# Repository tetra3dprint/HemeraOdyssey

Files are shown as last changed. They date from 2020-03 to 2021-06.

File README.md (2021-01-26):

## HemeraOdyssey **BETA** (v1.0)
Universal E3D Hemera mod for the Prusa i3 MK2 MK2.5 MK2.5S MK3 MK3S + Other variants  
This is for advanced users so **please** fully read this [**README.md**](README.md) to avoid disappointment, frustration and missguided expectations!  
I make no claims about this mod, it simply satisfies the requirement of enabling the Hemera to be used on stock firmware, pass self test and XYZ calibration.

[F **HemeraOdyssey Facebook group**](https://www.facebook.com/groups/HemeraOdyssey/)

Find me on twitter @ [tetra3dprint](https://twitter.com/tetra3dprint) 

## What is this mod
This is a universal one fits all mod that enabled the use of the E3D Hemera extruder on a Prusa i3 MK2/S MK2.5/S MK3/S without needing custom firmware (sort of).  
It will pass the self-test and XYZ calibration thanks to the geometry matching the stock setup but needs a minimum change to the e-steps that can be done via gcode.  
There is no loss in build volume.  
It supports both Laser and IR filament sensors.  
This is a very maintainable and moddable mod. I encourage and look forward to seeing mods and remixes, remeber to use the tag #hemeraodyssey

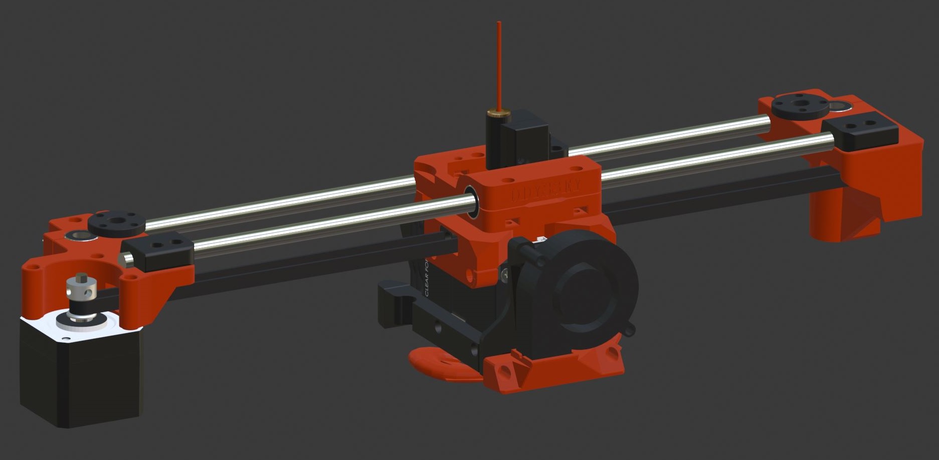
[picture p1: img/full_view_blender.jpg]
Hemera Odyssey Full View
  

|Document|Link|
|---:|:---|
|BOM|[**BOM**](BOM_Condensed.md)|
|Blender Source|[**HemeraOdysseyBlenderFile.zip**](../../raw/master/HemeraOdysseyBlenderFile.zip)
|**please read** Printing Guide|[**Printing Guide**](Print_Settings.md)|
|Build guide|[**Build guide**](Build_Guide/00_First.md)|
|Want to support this mod?|[**Click me**](#lots-of-coffee-and-filament-consumption)|

## This is a **BETA** mod!
I have to stress this is a **beta** mod with beta documentation.  
Parts might change over the next few weeks, please check everything and don't assume.  
I will make a note of changes in the assembly guide where relevant.  
You can also check for listed changes [**here**](Build_Guide/00_First.md#changes-in-beta-printed-parts)  
  
Documentation is not complete and will be updated daily until this message is gone.  
There are probably spelling and grammar mistakes and possibly incorrect links and numbers.   
Field testing of parts and printing parts is **limited**.
Some parts might cause problems when printing especially with materials I haven't tested.
I will attempt to deal with any highlighted issue in a timely fasion, that said, changes will be kept to a minimum if possible.

## Please respect the [**LICENSE**](LICENSE) this mod is released under
Please respect the GNU General Public License v3.0 that this mod is released under. This is the same license that Prusa use.

## MMU2 Support?
Not yet supported, however it is intended, but will require custom modified firmware which will come at a later date.

## No custom firmware (sort of)???!!!
Aside from needing to change the e-steps, this will work with stock firmware but it's not ideal.
The menu unload can cause a blob of filament to be pinched off below the hobbed gears. This in turn causes a filament jam that would then need clearing by dismantling the extruder.
On the MK3, the e-current will need to be increased slightly because the motor is 1.3A vs stock at 1.0A otherwise a moiré pattern is more visible than usual.

## Caveats
I showed a preview of my mod and there was a voice of concern in regard to the center of mass moving forward on the X carriage.  
This was mainly because the X motor is now positioned forward compared to stock.  
The concern is that this now unfavorably loads the z axis bearing and in turn reduces the life of the bearings and smooth rods.  
I have not been able to find data that supports or refutes this concern, however it does appear that the extra loading is within spec.  
So what does this mean? It might, or might not reduce the life of your z axis bearings and smooth rods.

The x carriage is slightly heavier than stock so this could manifest as more ghosting from x movements. Print settings can be adjusted to counter this.  
Here is a weight comparison of fully assembled variants of extruders: -  
|Extruder|~Weight(g)|
|---:|---:|
|Bondtech MK3|567|
|Stock MK2.5|630|
|Hemera Odyssey|697|

## Lots of coffee and filament consumption
In making this mod I've used several rolls of filament and drank lots of Grumpy Mule coffee. If you like it and want to support me in some way (obviously no obligation) maybe consider [**buying me a coffee here :)**](https://www.buymeacoffee.com/tetra3dprint)    

## Huge thanks to  
 
[Vlastimil Hovan on twitter](https://twitter.com/Vlastimil_Hovan)  
Vlastimil has kindly beta tested my mod, printed several variations and tried them out on his machines. He has also has given invaluable suggestions and feedback that have made their way back into the design.  
Not only that but he has created the first official mod (Z Tops) for my mod that enables the use on the MK3S variant, so huge respect and thanks to him.  
   
[Grégoire Saunier #BearUpgrade on twitter](https://twitter.com/GregoireSaunier)  
Grégoire has not only been inspiration but has also been kind enough to offer some guidance here and there that kept me on the straight and narrow :) so huge respect and thanks to him. 

## Blender Source Files
I used Blender to create the files for this mod so only the blender file and STL files will are available.  
The blender file is available at the root of this repo here [**HemeraOdysseyBlenderFile.zip**](../../raw/master/HemeraOdysseyBlenderFile.zip)

## Sources
* Prusa: http://www.prusa3d.com
* E3D Hemera: https://e3d-online.com/
* Grégoire Saunier : https://github.com/gregsaun/
* Blender 3D: https://www.blender.org/

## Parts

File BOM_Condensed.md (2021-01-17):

# Hemera Odyssey Beta

## Bill of Materials

### Hardware

| Part | Quantity | Detail | Example Links |
|---|:---:|---|---|
| Original Prusa i3 MK2(S) or MK2.5(S) or MK3(S) | 1 | :warning: MK2 or MK3 (non-S) also usable | [Prusa](https://www.prusa3d.com) |
| E3D Hemera Direct Kit (1.75mm) | 1 | | [E3D-ONLINE](https://e3d-online.com/collections/hotends/products/e3d-hemera-direct-kit-1-75mm)|
| M3x8mm socket head screw (ISO 4762) | 4 | | [McMaster-Carr](https://www.mcmaster.com/91292A112/) |
| M3x10mm socket head screw (ISO 4762) | 7 | | [McMaster-Carr](https://www.mcmaster.com/91292A113/) |
| M3x14mm socket head screw (ISO 4762) | 21| | [McMaster-Carr](https://www.mcmaster.com/91292A027/) |
| M3x16mm socket head screw (ISO 4762) | 2 | | [McMaster-Carr](https://www.mcmaster.com/91292A115/) |
| M3x18mm socket head screw (ISO 4762) | 9 | | [McMaster-Carr](https://www.mcmaster.com/91292A029/) |
| M3x25mm socket head screw (ISO 4762) | 2 | | [McMaster-Carr](https://www.mcmaster.com/91292A020/) |
| M3x40mm socket head screw (ISO 4762) | 1 | | [McMaster-Carr](https://www.mcmaster.com/91292A024/) |
| M3 hex nuts DIN 934 | 10| | [McMaster-Carr](https://www.mcmaster.com/91828A211/) |
| M3 square nut DIN 562 | 14| | [McMaster-Carr](https://www.mcmaster.com/97258A101/) |
| M3 thin square nut (Hemera) | 4 | | [E3D-ONLINE](https://e3d-online.com/products/e3d-hemera-fixings-kit) |
| M3 nylock nut DIN 985 | 6 | | [McMaster-Carr](https://www.mcmaster.com/93625a100) |
| M3 flat washer (ISO 7089) | 2 | | [McMaster-Carr](https://www.mcmaster.com/93475A210/) |
| Zip ties 2.5x100mm | 7 | | |
| 1.75mm PTFE Tube (43mm.L) | 1 | | |
| 1.75mm PTFE Tube (11mm.L) - Laser sensor | 1 | :warning: Only for MK2 or MK3 (non-S) | |
 
### Optional

| Part | Quantity | Detail | Example Links |
|---|:---:|---|---|
| 4.95mm OD Dowel (14-15.8mm) | 1 | for Gates Idler | |
| Toothed T20 Gates Idler | 1 | | |
| M5 Threaded Brass Insert | 1 | | |
 
### Printed Parts

| Part | Quantity | Comment |
|---|:---:|---|
| [Filament_Sensor_IR_Cover](HemeraOdyssey_STLs_BETA/HemeraOdyssey-Filament_Sensor_IR_Cover.stl) | 1 | :warning: Only for MK2.5(S) or MK3(S)|
| [Filament_Sensor_IR_Housing](HemeraOdyssey_STLs_BETA/HemeraOdyssey-Filament_Sensor_IR_Housing.stl) | 1 | :warning: Only for MK2.5(S) or MK3(S)|
| [Filament_Sensor_IR_Spring](HemeraOdyssey_STLs_BETA/HemeraOdyssey-Filament_Sensor_IR_Spring.stl) | 1 | :warning: Only for MK2.5(S) or MK3(S)|
| [Filament_Sensor_IR_Trigger](HemeraOdyssey_STLs_BETA/HemeraOdyssey-Filament_Sensor_IR_Trigger.stl) | 1 | :warning: Only for MK2.5(S) or MK3(S)|
| [Filament_Sensor_Laser_Housing](HemeraOdyssey_STLs_BETA/HemeraOdyssey-Filament_Sensor_Laser_Housing.stl) | 1 | |
| [Filament_Sensor_Laser_Lid](HemeraOdyssey_STLs_BETA/HemeraOdyssey-Filament_Sensor_Laser_Lid.stl) | 1 | |
| [Filament_Sensor_Laser_Wahser](HemeraOdyssey_STLs_BETA/HemeraOdyssey-Filament_Sensor_Laser_Wahser.stl) | 1 | |
| [Idler_Housing_Prusa](HemeraOdyssey_STLs_BETA/HemeraOdyssey-Idler_Housing_Prusa_20T_3mmID.stl) | 1 | |
| [Idler_Housing_Prusa_Bottom](HemeraOdyssey_STLs_BETA/HemeraOdyssey-Idler_Housing_Prusa_20T_3mmID_Spacer_Bottom.stl)| 1 | :warning: Print a single part|
| [Idler_Housing_Prusa_Top](HemeraOdyssey_STLs_BETA/HemeraOdyssey-Idler_Housing_Prusa_20T_3mmID_Spacer_Top.stl) | 1 | :warning: Print a single part|
| [Nozzle_Fang](HemeraOdyssey_STLs_BETA/HemeraOdyssey-Nozzle_Fang.stl) | 1 | :warning: Print a single part |
| [Part_Left_Front_Rod_Clamp](HemeraOdyssey_STLs_BETA/HemeraOdyssey-Part_Left_Front_Rod_Clamp.stl) | 1 | |
| [Part_Left_Motor](HemeraOdyssey_STLs_BETA/HemeraOdyssey-Part_Left_Motor.stl) | 1 | :warning: Print a single part |
| [Part_Right_Front_Rod_Clamp](HemeraOdyssey_STLs_BETA/HemeraOdyssey-Part_Right_Front_Rod_Clamp.stl) | 1 | |
| [Part_Right_Idler](HemeraOdyssey_STLs_BETA/HemeraOdyssey-Part_Right_Idler.stl) | 1 | :warning: Print a single part |
| [Undercarriage_Back](HemeraOdyssey_STLs_BETA/HemeraOdyssey-Undercarriage_Back.stl) | 1 | |
| [Undercarriage_Back_Cap](HemeraOdyssey_STLs_BETA/HemeraOdyssey-Undercarriage_Back_Cap.stl) | 1 | |
| [Undercarriage_Fan_Mount](HemeraOdyssey_STLs_BETA/HemeraOdyssey-Undercarriage_Fan_Mount.stl) | 1 | |
| [Undercarriage_Left](HemeraOdyssey_STLs_BETA/HemeraOdyssey-Undercarriage_Left.stl) | 1 | |
| [Undercarriage_Right](HemeraOdyssey_STLs_BETA/HemeraOdyssey-Undercarriage_Right.stl) | 1 | |
| [X_Carriage](HemeraOdyssey_STLs_BETA/HemeraOdyssey-X_Carriage.stl) | 1 | :warning: Print a single part |
| [X_Carriage_Belt_Tensioner_Left](HemeraOdyssey_STLs_BETA/HemeraOdyssey-X_Carriage_Belt_Tensioner_Left.stl) | 1 | |
| [X_Carriage_Belt_Tensioner_Right](HemeraOdyssey_STLs_BETA/HemeraOdyssey-X_Carriage_Belt_Tensioner_Right.stl) | 1 | |
| [X_Carriage_Washer](HemeraOdyssey_STLs_BETA/HemeraOdyssey-X_Carriage_Washer.stl) | 1 | :warning: Print a single part |
| [Z_Top_Left_7mm_MK3S_MK2_5S](HemeraOdyssey_STLs_BETA/HemeraOdyssey-Z_Top_Left_7mm_MK3S_MK2_5S.stl) | 1 | :warning: Only for MK2.5(S) or MK3(S)|

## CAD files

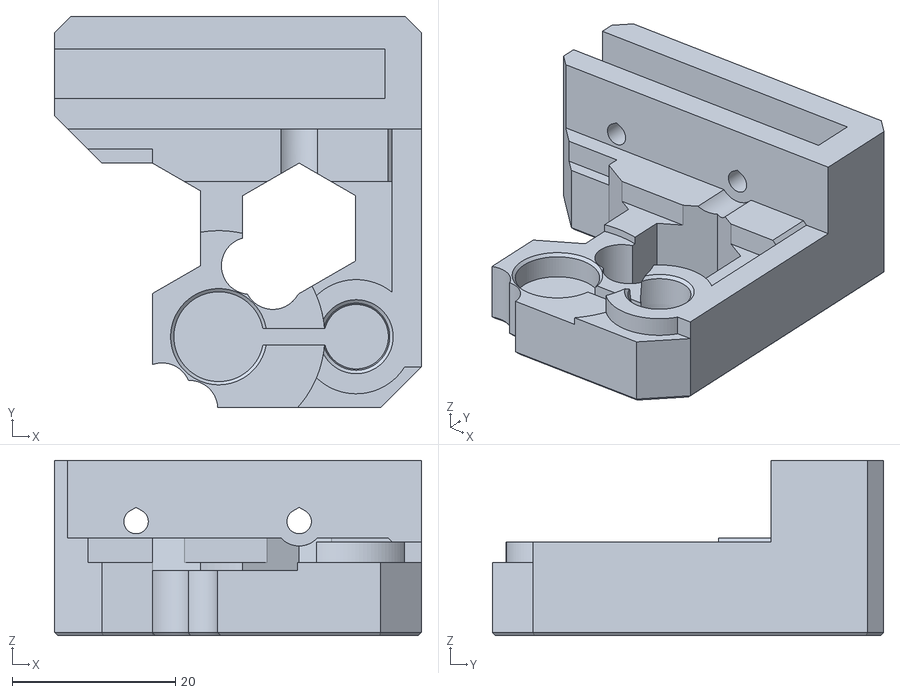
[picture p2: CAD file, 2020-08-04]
HemeraOdyssey_STLs_BETA/HemeraOdyssey-Z_Top_Left_7mm_MK3S_MK2_5S.stl
45.0 x 48.0 x 21.5

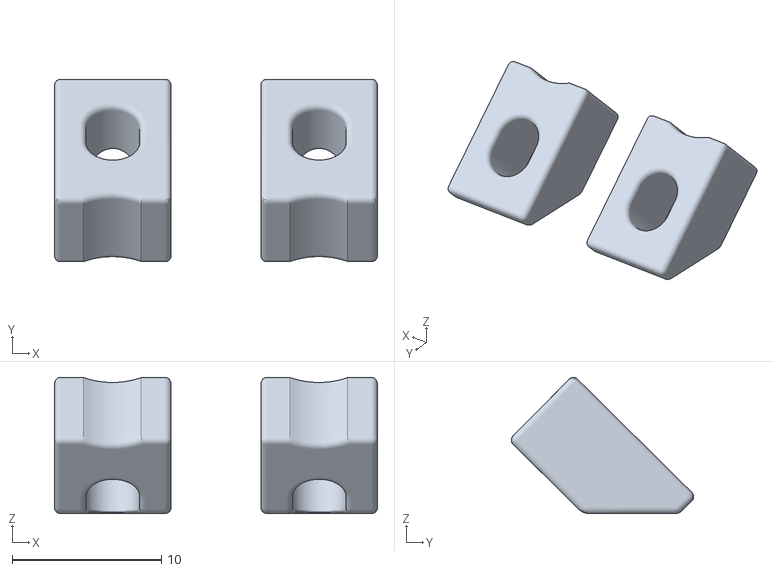
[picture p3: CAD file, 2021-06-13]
HemeraOdyssey_STLs_v01_75/HemeraOdyssey-Rear_Rod_Wedge-01_75.stl
21.6 x 12.2 x 9.12

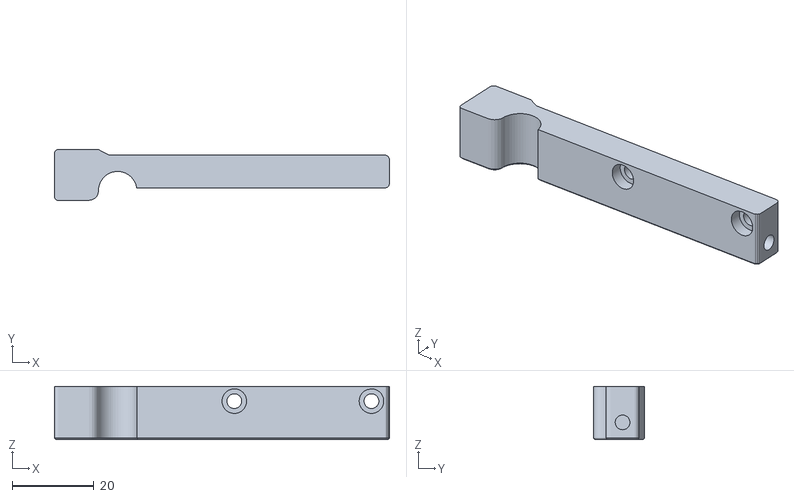
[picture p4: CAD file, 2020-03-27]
HemeraOdyssey_STLs_BETA/HemeraOdyssey-Undercarriage_Left.stl
81.9 x 12.5 x 13.1

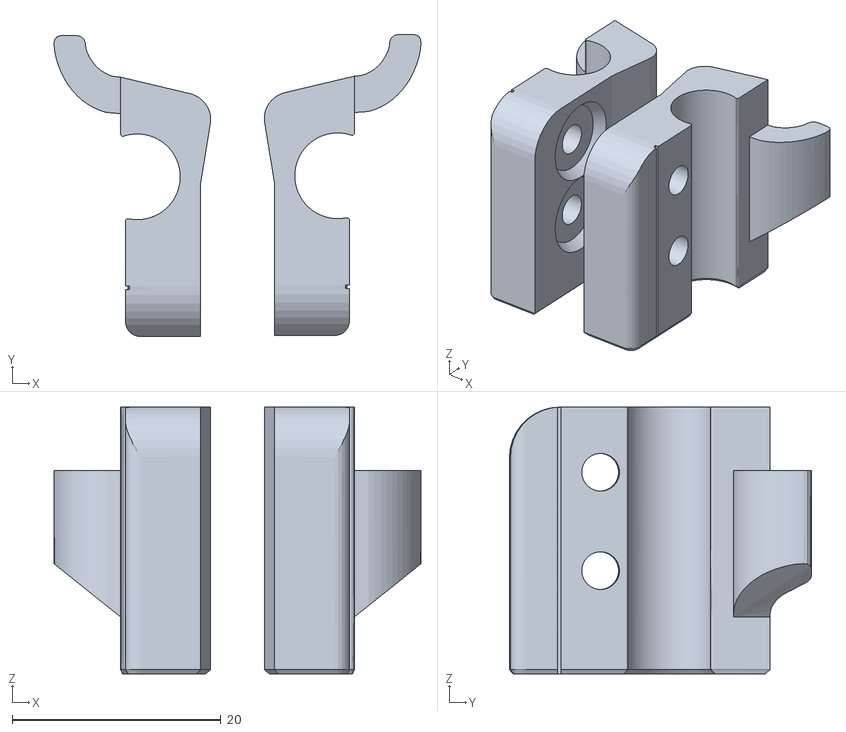
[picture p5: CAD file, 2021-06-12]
HemeraOdyssey_STLs_v01_75/HemeraOdyssey-Part_Front_Rod_Clamps-01_75.stl
35.1 x 28.9 x 25.5

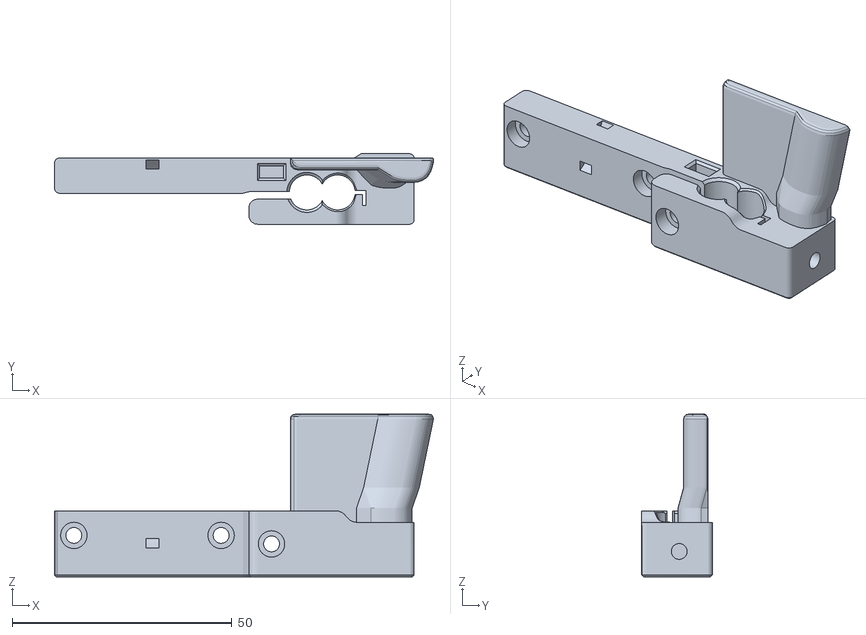
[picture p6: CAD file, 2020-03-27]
HemeraOdyssey_STLs_BETA/HemeraOdyssey-Undercarriage_Right.stl
86.2 x 16.0 x 37.0

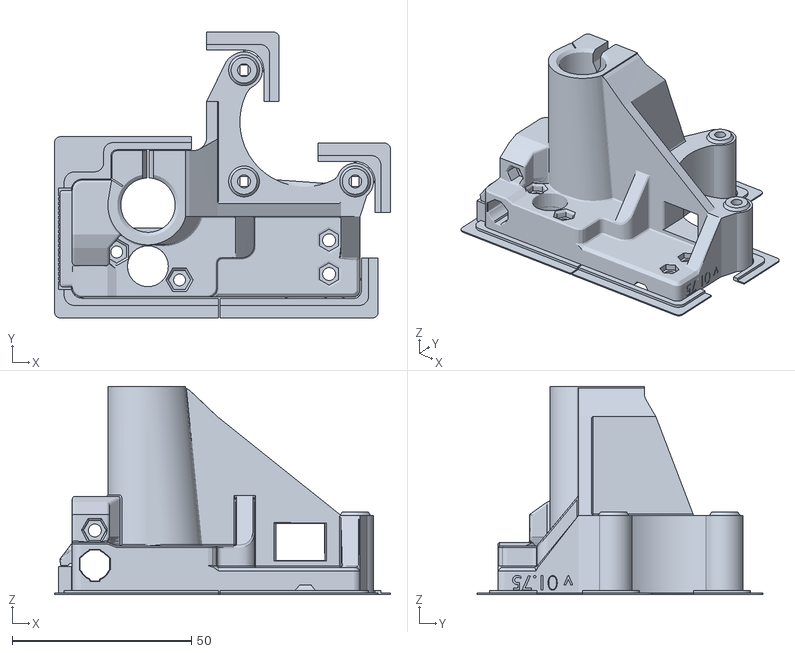
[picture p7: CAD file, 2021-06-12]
HemeraOdyssey_STLs_v01_75/HemeraOdyssey-Part_Left_Motor-01_75.stl
93.7 x 79.7 x 58.0

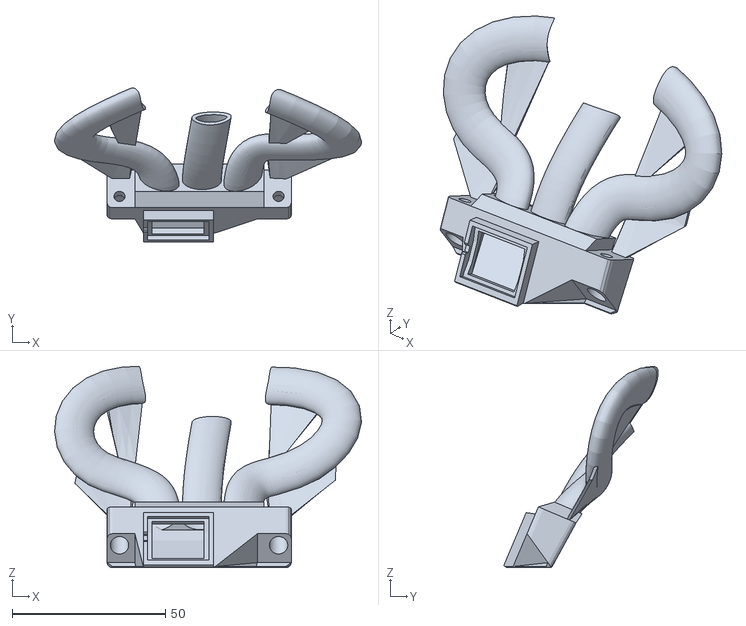
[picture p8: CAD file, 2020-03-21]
HemeraOdyssey_STLs_BETA/HemeraOdyssey-Nozzle_Fang.stl
100.2 x 50.4 x 65.7

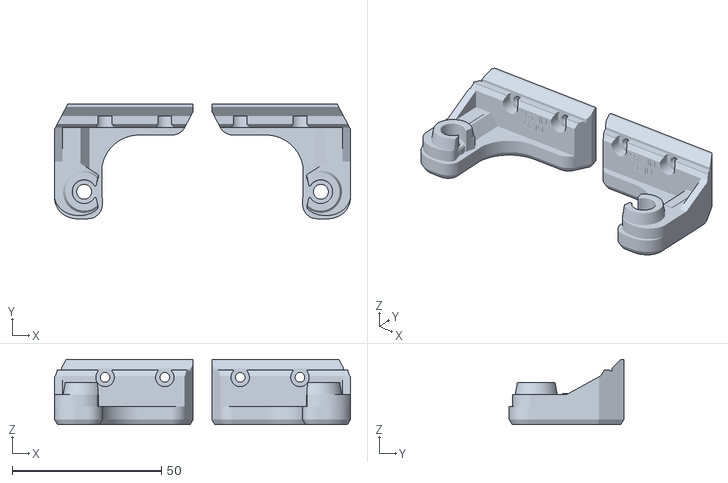
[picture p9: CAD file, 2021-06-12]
HemeraOdyssey_STLs_v01_75/HemeraOdyssey-Z_Tops_Final_MK3S_MK2_5S-01_75.stl
99.1 x 38.3 x 21.8

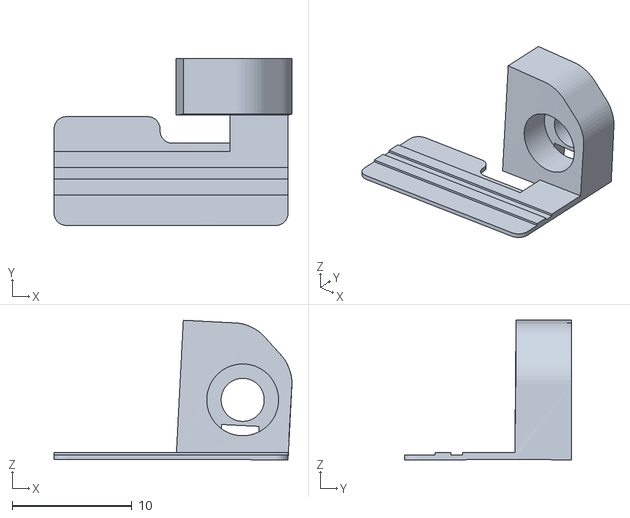
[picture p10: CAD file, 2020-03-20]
HemeraOdyssey_STLs_BETA/HemeraOdyssey-Filament_Sensor_IR_Spring.stl
19.9 x 14.0 x 11.7

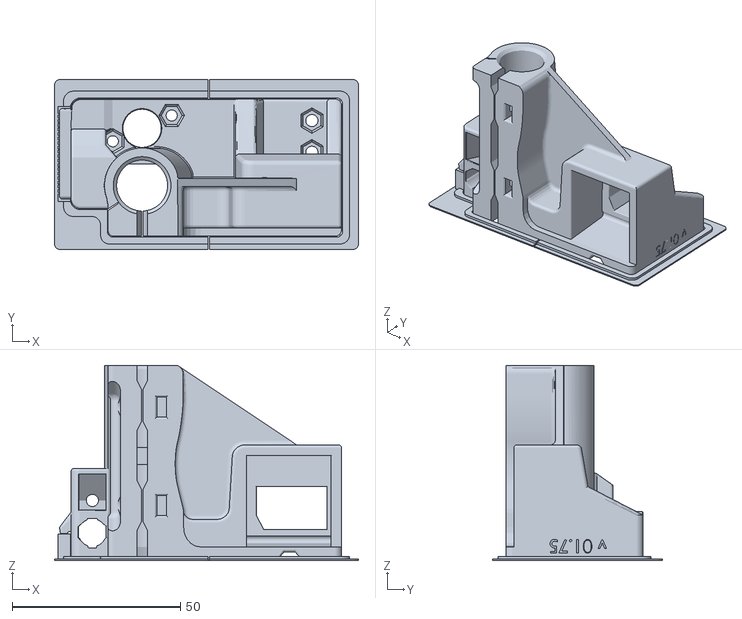
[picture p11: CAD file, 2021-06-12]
HemeraOdyssey_STLs_v01_75/HemeraOdyssey-Part_Right_Idler-01_75.stl
90.4 x 50.6 x 58.0

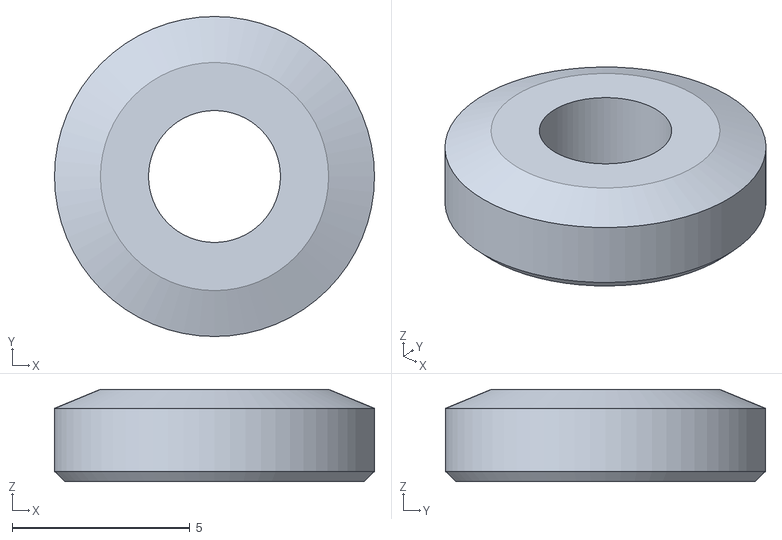
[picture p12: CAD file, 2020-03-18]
HemeraOdyssey_STLs_BETA/HemeraOdyssey-Idler_Housing_Prusa_20T_3mmID_Spacer_Bottom.stl
9.00 x 9.00 x 2.60

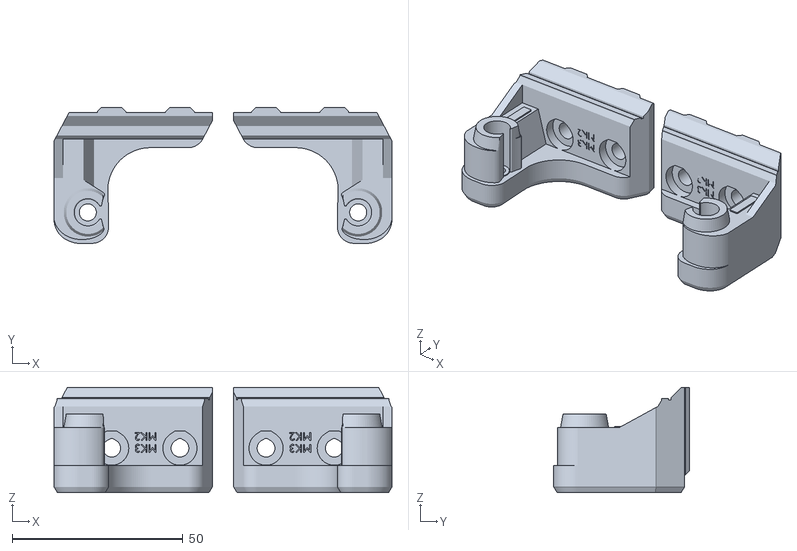
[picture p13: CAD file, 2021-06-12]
HemeraOdyssey_STLs_v01_75/HemeraOdyssey-Z_Tops_Final_MK3_MK2_Bear-01_75.stl
99.1 x 39.8 x 30.8

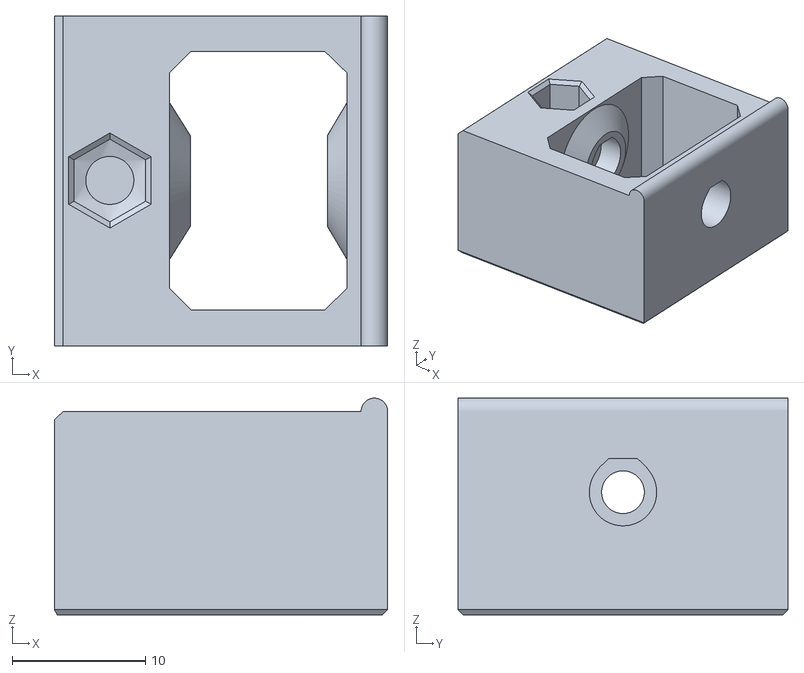
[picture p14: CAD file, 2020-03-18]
HemeraOdyssey_STLs_BETA/HemeraOdyssey-Idler_Housing_Gates_20T_5mmID.stl
25.0 x 24.7 x 16.2

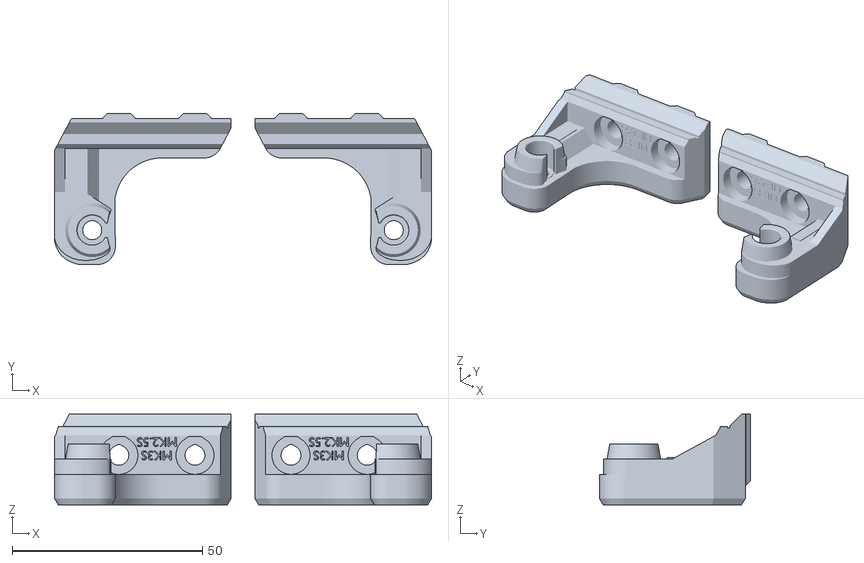
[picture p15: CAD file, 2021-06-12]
HemeraOdyssey_STLs_v01_75/HemeraOdyssey-Z_Tops_Final_MK3S_MK2_5S_Bear-01_75.stl
99.1 x 39.8 x 23.8

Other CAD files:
HemeraOdyssey_STLs_BETA/HemeraOdyssey-Z_Top_Right_7mm_MK3S_MK2_5S.stl
HemeraOdyssey_STLs_BETA/HemeraOdyssey-Part_Right_Idler.stl
HemeraOdyssey_STLs_v01_75/HemeraOdyssey-X_Carriage_Combo-01_75.stl
HemeraOdyssey_STLs_BETA/HemeraOdyssey-Idler_Housing_Prusa_20T_3mmID.stl
HemeraOdyssey_STLs_BETA/HemeraOdyssey-Filament_Sensor_IR_Cover.stl
HemeraOdyssey_STLs_BETA/HemeraOdyssey-Filament_Sensor_IR_Housing.stl
HemeraOdyssey_STLs_BETA/HemeraOdyssey-Filament_Sensor_IR_Trigger.stl
HemeraOdyssey_STLs_BETA/HemeraOdyssey-Filament_Sensor_Laser_Housing.stl
HemeraOdyssey_STLs_BETA/HemeraOdyssey-Filament_Sensor_Laser_Lid.stl
HemeraOdyssey_STLs_BETA/HemeraOdyssey-Filament_Sensor_Laser_Wahser.stl
HemeraOdyssey_STLs_BETA/HemeraOdyssey-Idler_Housing_Prusa_20T_3mmID_Spacer_Top.stl
HemeraOdyssey_STLs_BETA/HemeraOdyssey-Part_Left_Front_Rod_Clamp.stl
HemeraOdyssey_STLs_BETA/HemeraOdyssey-Part_Left_Motor.stl
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

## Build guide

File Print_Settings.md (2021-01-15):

# Hemera Odyssey Print Settings

### #hemeraodyssey

* Use PETG for all part
* Part are already correctly orientated to take best advantage of stock part cooling, do not change the orientation
* Use exactly 4 perimeters @ (Prusa Slic3r default) 0.45mm width, change other slicers to this.
* Use 0.2mm layer height
* Use at least 20% rectangular infill
* Supports and brims are **not** required

| Part | Quantity | Layer<br/>Height<br/>[mm] | Infill [%] | Num.<br/>Perimeters | Num.<br/>Top / Bottom<br/>Layers | Note |
|:-----|:---:|:---:|:---:|:---:|:---:|:-----|
| [**Filament_Sensor_IR_Cover**](HemeraOdyssey_STLs_BETA/HemeraOdyssey-Filament_Sensor_IR_Cover.stl) | 1 | 0.20 | 20 | 4 | 5 | :warning: Only for MK2.5(S) or MK3(S)|
| [**Filament_Sensor_IR_Housing**](HemeraOdyssey_STLs_BETA/HemeraOdyssey-Filament_Sensor_IR_Housing.stl) | 1 | 0.20 | 20 | 4 | 5 | :warning: Only for MK2.5(S) or MK3(S)|
| [**Filament_Sensor_IR_Spring**](HemeraOdyssey_STLs_BETA/HemeraOdyssey-Filament_Sensor_IR_Spring.stl) | 1 | 0.20 | 20 | 4 | 5 | :warning: Only for MK2.5(S) or MK3(S)|
| [**Filament_Sensor_IR_Trigger**](HemeraOdyssey_STLs_BETA/HemeraOdyssey-Filament_Sensor_IR_Trigger.stl) | 1 | 0.20 | 20 | 4 | 5 | :warning: Only for MK2.5(S) or MK3(S)|
| [**Filament_Sensor_Laser_Housing**](HemeraOdyssey_STLs_BETA/HemeraOdyssey-Filament_Sensor_Laser_Housing.stl) | 1 | 0.20 | 20 | 4 | 5 | |
| [**Filament_Sensor_Laser_Lid**](HemeraOdyssey_STLs_BETA/HemeraOdyssey-Filament_Sensor_Laser_Lid.stl) | 1 | 0.20 | 20 | 4 | 5 | |
| [**Filament_Sensor_Laser_Wahser**](HemeraOdyssey_STLs_BETA/HemeraOdyssey-Filament_Sensor_Laser_Wahser.stl) | 1 | 0.20 | 20 | 4 | 5 | |
| [**Idler_Housing_Prusa**](HemeraOdyssey_STLs_BETA/HemeraOdyssey-Idler_Housing_Prusa_20T_3mmID.stl) | 1 | 0.20 | 20 | 4 | 5 | |
| [**Idler_Housing_Prusa_Bottom**](HemeraOdyssey_STLs_BETA/HemeraOdyssey-Idler_Housing_Prusa_20T_3mmID_Spacer_Bottom.stl)| 1 | 0.20 | 20 | 4 | 5 | :warning: Print a single part|
| [**Idler_Housing_Prusa_Top**](HemeraOdyssey_STLs_BETA/HemeraOdyssey-Idler_Housing_Prusa_20T_3mmID_Spacer_Top.stl) | 1 | 0.20 | 20 | 4 | 5 | :warning: Print a single part|
| [**Nozzle_Fang**](HemeraOdyssey_STLs_BETA/HemeraOdyssey-Nozzle_Fang.stl) | 1 | 0.20 | 20 | 4 | 5 | :warning: Print a single part |
| [**Part_Left_Front_Rod_Clamp**](HemeraOdyssey_STLs_BETA/HemeraOdyssey-Part_Left_Front_Rod_Clamp.stl) | 1 | 0.20 | 20 | 4 | 5 | |
| [**Part_Left_Motor**](HemeraOdyssey_STLs_BETA/HemeraOdyssey-Part_Left_Motor.stl) | 1 | 0.20 | 20 | 4 | 5 | :warning: Print a single part |
| [**Part_Right_Front_Rod_Clamp**](HemeraOdyssey_STLs_BETA/HemeraOdyssey-Part_Right_Front_Rod_Clamp.stl) | 1 | 0.20 | 20 | 4 | 5 | |
| [**Part_Right_Idler**](HemeraOdyssey_STLs_BETA/HemeraOdyssey-Part_Right_Idler.stl) | 1 | 0.20 | 20 | 4 | 5 | :warning: Print a single part |
| [**Undercarriage_Back**](HemeraOdyssey_STLs_BETA/HemeraOdyssey-Undercarriage_Back.stl) | 1 | 0.20 | 20 | 4 | 5 | |
| [**Undercarriage_Back_Cap**](HemeraOdyssey_STLs_BETA/HemeraOdyssey-Undercarriage_Back_Cap.stl) | 1 | 0.20 | 20 | 4 | 5 | |
| [**Undercarriage_Fan_Mount**](HemeraOdyssey_STLs_BETA/HemeraOdyssey-Undercarriage_Fan_Mount.stl) | 1 | 0.20 | 20 | 4 | 5 | |
| [**Undercarriage_Left**](HemeraOdyssey_STLs_BETA/HemeraOdyssey-Undercarriage_Left.stl) | 1 | 0.20 | 20 | 4 | 5 | |
| [**Undercarriage_Right**](HemeraOdyssey_STLs_BETA/HemeraOdyssey-Undercarriage_Right.stl) | 1 | 0.20 | 20 | 4 | 5 | |
| [**X_Carriage**](HemeraOdyssey_STLs_BETA/HemeraOdyssey-X_Carriage.stl) | 1 | 0.20 | 20 | 4 | 5 | :warning: Print a single part |
| [**X_Carriage_Belt_Tensioner_Left**](HemeraOdyssey_STLs_BETA/HemeraOdyssey-X_Carriage_Belt_Tensioner_Left.stl) | 1 | 0.20 | 20 | 4 | 5 | |
| [**X_Carriage_Belt_Tensioner_Right**](HemeraOdyssey_STLs_BETA/HemeraOdyssey-X_Carriage_Belt_Tensioner_Right.stl) | 1 | 0.20 | 20 | 4 | 5 | |
| [**X_Carriage_Washer**](HemeraOdyssey_STLs_BETA/HemeraOdyssey-X_Carriage_Washer.stl) | 1 | 0.20 | 20 | 4 | 5 | :warning: Print a single part |
| [**Z_Top_Left_7mm_MK3S_MK2_5S**](HemeraOdyssey_STLs_BETA/HemeraOdyssey-Z_Top_Left_7mm_MK3S_MK2_5S.stl) | 1 | 0.20 | 20 | 4 | 5 | :warning: Only for MK2.5(S) or MK3(S)|
| [**Z_Top_Right_7mm_MK3S_MK2_5S**](HemeraOdyssey_STLs_BETA/HemeraOdyssey-Z_Top_Right_7mm_MK3S_MK2_5S.stl) | 1 | 0.20 | 20 | 4 | 5 | :warning: Only for MK2.5(S) or MK3(S)|

### #optional

| Part | Quantity | Layer<br/>Height<br/>[mm] | Infill [%] | Num.<br/>Perimeters | Num.<br/>Top / Bottom<br/>Layers | Note |
|:-----|:---:|:---:|:---:|:---:|:---:|:-----|
| [**Idler_Housing_Gates_20T**](HemeraOdyssey_STLs_BETA/HemeraOdyssey-Idler_Housing_Gates_20T_5mmID.stl) | 1 | 0.20 | 20 | 4 | 5 | :warning: Only for Gates Toothed T20 |

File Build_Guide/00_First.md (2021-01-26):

 | [Next](01_Part_Left.md)  
---
* **Do not over tighten anything!!**
* When screwing into plastic, take it slowly with firm pressure and be mindfull not to over tighten
* You will need a suitable hex driver
* The Hemera comes with some hardware like 8mm M3 + more
* Some hardware comes from disassembling the current x carriage
* Some hardware will have to be purchased like the 14mm M3 and I recommend getting some spare square, hex and nylon hex nuts
* The mod suppors thick or thin M3 square nuts
<br>  

## Printed part cleanup requirements
* Some part have snap off brim/supports that may require a little clean up
* Some holes need to be punctured using the hex driver due to the bridging support
* The rear smooth rod clamps have built in support that needs to be removed carefully using a knife or thin metal ruler. This is made easier by inserting and removing a smooth rod before hand.  
<br>  

## Changes in BETA printed parts
Updated ztops for MK3S and MK2.5S, there was an error in the model that caused XYZ calibration to fail from Z height.  
[**HemeraOdyssey-Z_Top_Left_7mm_MK3S_MK2_5S.stl**](../HemeraOdyssey_STLs_BETA/HemeraOdyssey-Z_Top_Left_7mm_MK3S_MK2_5S.stl)  
[**HemeraOdyssey-Z_Top_Right_7mm_MK3S_MK2_5S.stl**](../HemeraOdyssey_STLs_BETA/HemeraOdyssey-Z_Top_Right_7mm_MK3S_MK2_5S.stl)  
<br>
The following parts changed from using 6mm to 8mm. This is because my "M-FIX-HERMES" bag contained both 6mm and 8mm and I picked 6mm. Turns out they should not have been there.  

[**HemeraOdyssey-Undercarriage_Left.stl**](../HemeraOdyssey_STLs_BETA/HemeraOdyssey-Undercarriage_Left.stl)  
[**HemeraOdyssey-Undercarriage_Right.stl**](../HemeraOdyssey_STLs_BETA/HemeraOdyssey-Undercarriage_Right.stl)  
<br>

## You must use the supplied Hemera heat sink fan

**Do not use the stock Prusa fan** it does **not** have enough static pressure and you will get endless jamms.
Unfortunately the supplied fan lacks a stall sensor that the Prusa firmware uses to detect the fan stalling, consequently you have to turn off fan check: -
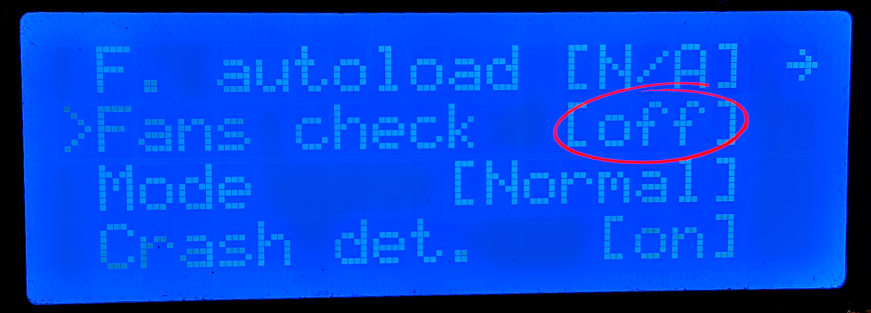
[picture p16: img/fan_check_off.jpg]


If you intend to run self test, then you will need to temporarily connect the original Prusa fan in order for the test to pass.
  
Connecting the provided fan to the MK3 requires you to connect the (black) ground as normal to the fan ground pin and the positive (red) goes to Pin 1 (+24v) of the J19 Raspberry Pi connector.
<br>
Check out the great guide from Grégoire Saunier #BearUpgrade [Here](https://guides.bear-lab.com/Guide/3.+BearMera+extruder/29?lang=en#s312)
<br>  
There are some suitable alternative fans, but a lot don't have the correct type of sensor. There is one suitable plug and play fan in development, but not available on the market yet afaik.
<br>
My HemeraOdyssey mod can support fans up to 15mm thick.
<br>
Personally I run a 5v 15mm with 6.35mm H2O static pressure but it does not have a rpm sensor. Instead the sense wire that's high when running and low when stalled.  
I made a small arduino sketch that monitors the fan then outputs a signal to the einsy that emulates 4500rpm while high and 0rpm while stalled.

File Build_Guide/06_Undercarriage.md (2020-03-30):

[Previous](05_Filament_Sensor.md) | [Next](07_Extruder.md)  
---
# Undercarriage
### #hemeraodyssey
---
# Parts  
|Quantity|Size|Type|
|---:|:---:|:---:|
|1|[**HemeraOdyssey-Undercarriage_Left.stl**](../HemeraOdyssey_STLs_BETA/HemeraOdyssey-Undercarriage_Left.stl)|Printed Part|
|1|[**HemeraOdyssey-Undercarriage_Right.stl**](../HemeraOdyssey_STLs_BETA/HemeraOdyssey-Undercarriage_Right.stl)|Printed Part|
|1|[**HemeraOdyssey-Undercarriage_Back.stl**](../HemeraOdyssey_STLs_BETA/HemeraOdyssey-Undercarriage_Back.stl)|Printed Part|
|5|M3|Square Nut|
|4|M3|Thin Square Nut (Hemera)|
|4|8mm (changed from 6mm)|M3 Bolt (Hemera)|
|1|10mm|M3 Bolt|
|2|14mm|M3 Bolt|
|1|40mm|M3 Bolt|
|1|M3|Hex Nylon Lock Nut|
---
### 01
* Ensure the Hemera is assembled according to [E3D build guide](https://e3d-online.dozuki.com/c/Hemera_Assembly_Guides)
* Do **not** use the stock Noctua fan, you will only get jamms
* The only recommended fan is the one provided with the Hemera, see [here](00_First.md) for more details<br>  
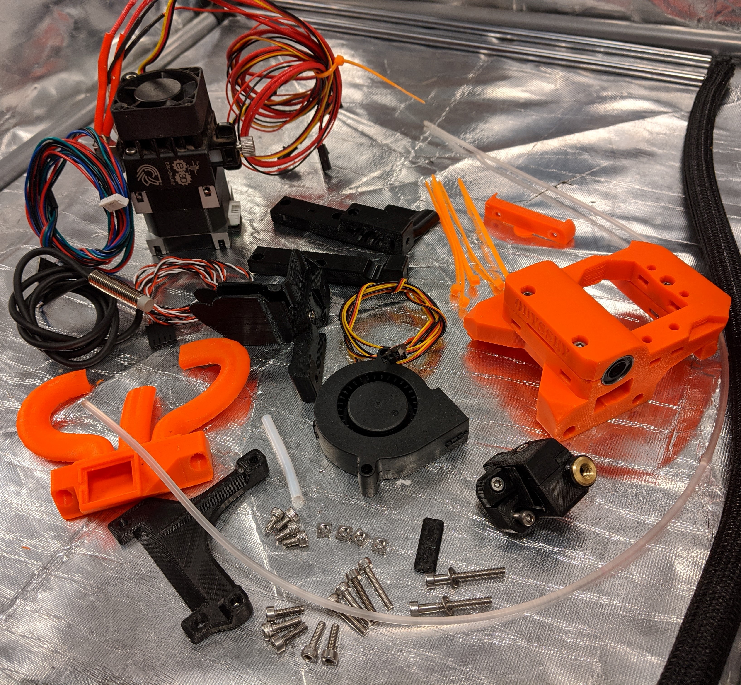
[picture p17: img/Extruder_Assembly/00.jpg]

---
### 02
* Insert 1x 40mm bolt into the undercarriage back and secure with a hex nylon lock nut, tighten completely
* This provides strength<br>  
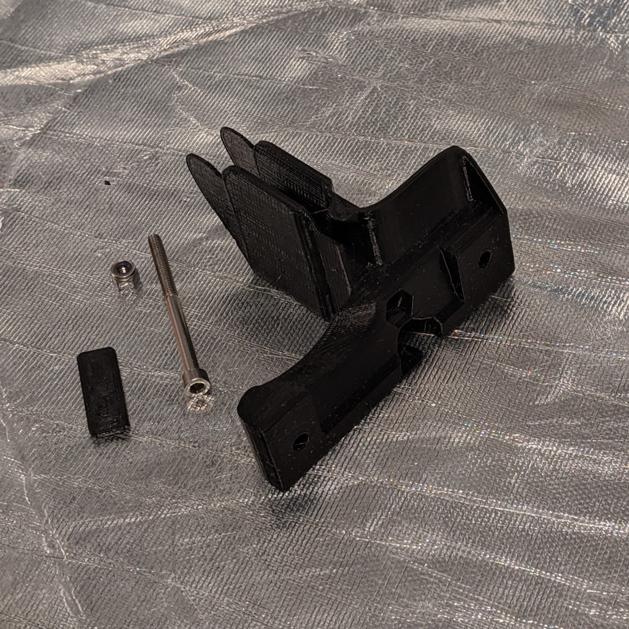
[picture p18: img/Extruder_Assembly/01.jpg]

---
### 03
* The undercarriage left requires 2x square nuts
* The undercarriage right requires 3x square nuts<br>  
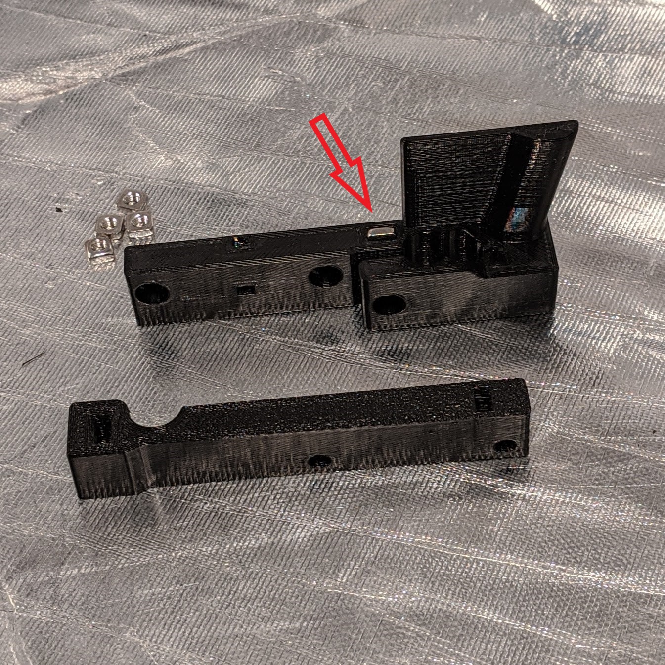
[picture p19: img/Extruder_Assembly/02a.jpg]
02a

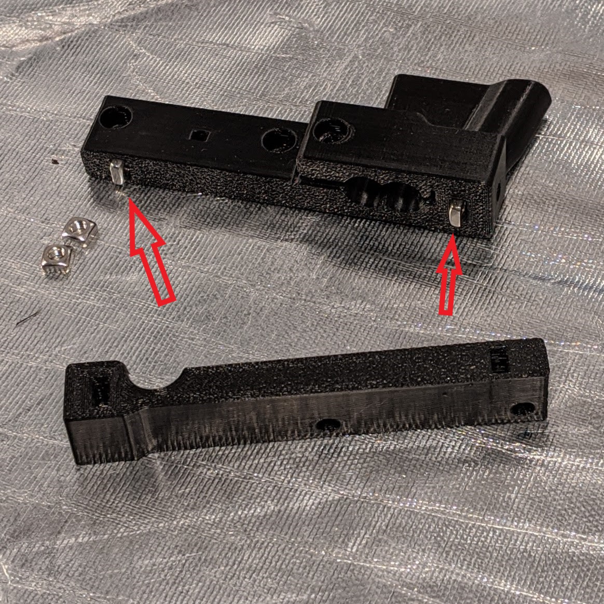
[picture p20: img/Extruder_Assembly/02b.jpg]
02b

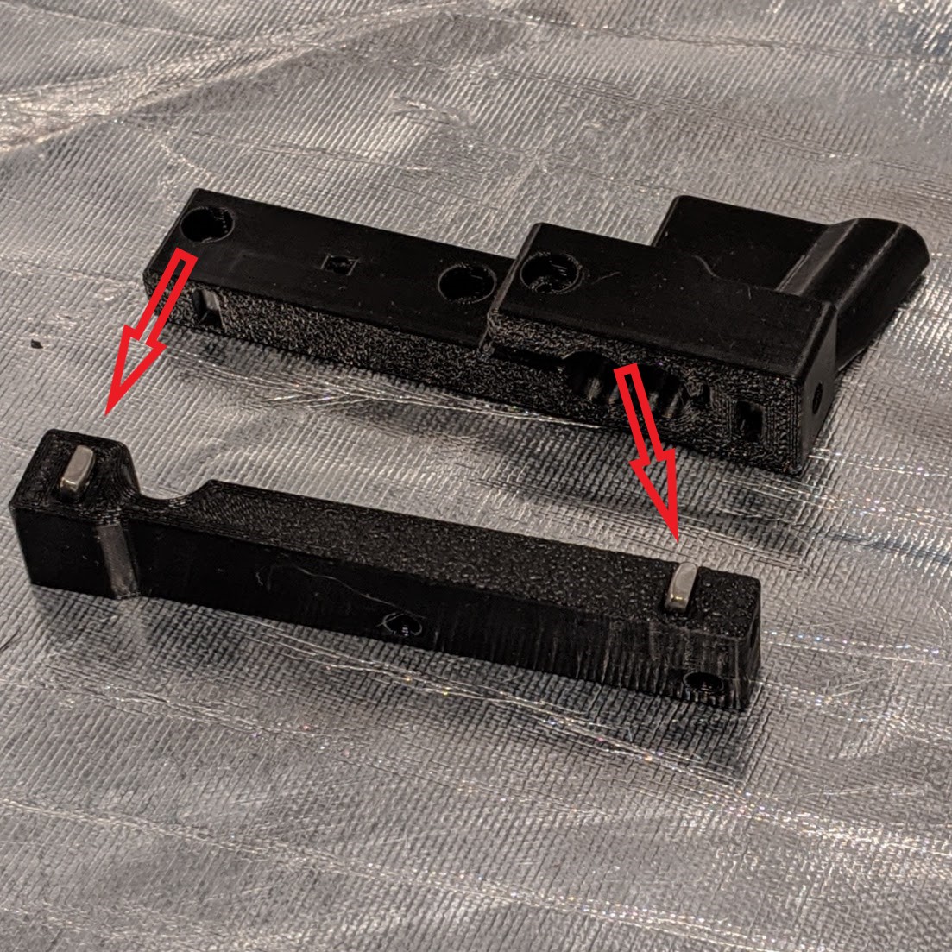
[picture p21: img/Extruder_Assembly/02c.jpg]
02c

---
### 04
* **Warning**, make sure you use the most recent vesrsion of the Undercarriage Left, the old version used 6mm instead of 8mm!!!
* Insert 1x thin square nut into the hemera mounting hole and secure the undercarriage left with 2x 8mm bolts<br>  
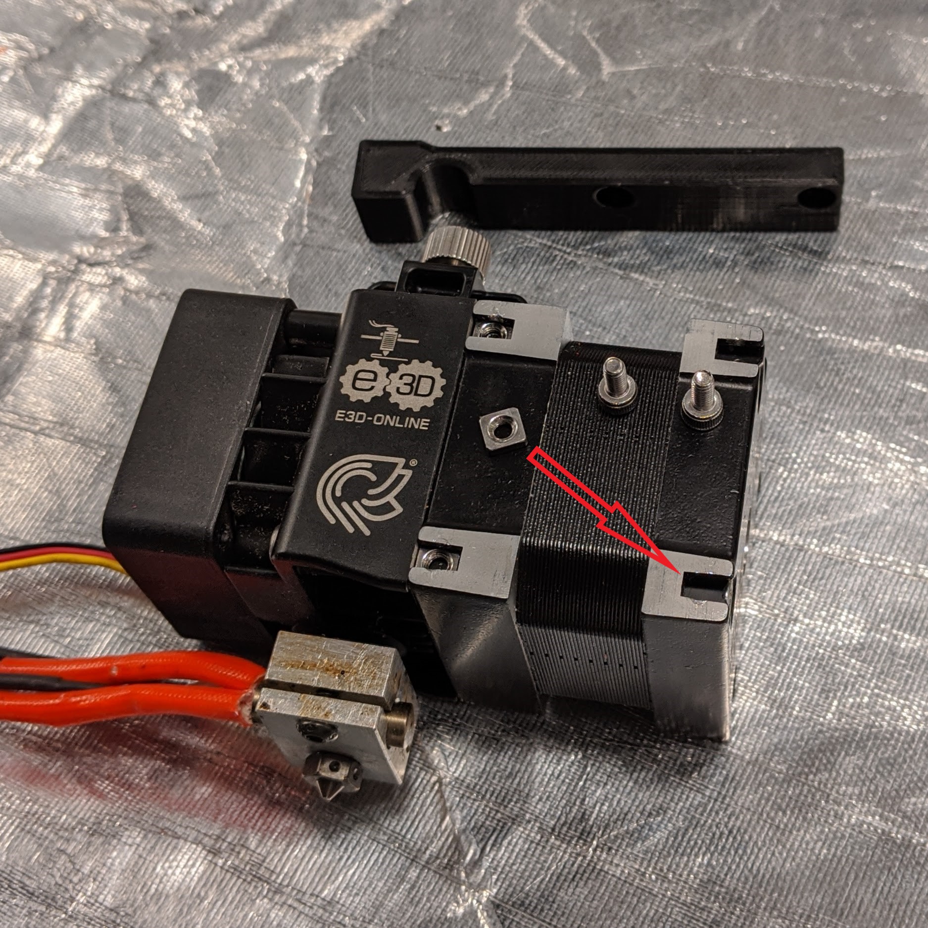
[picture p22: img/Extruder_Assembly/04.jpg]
 
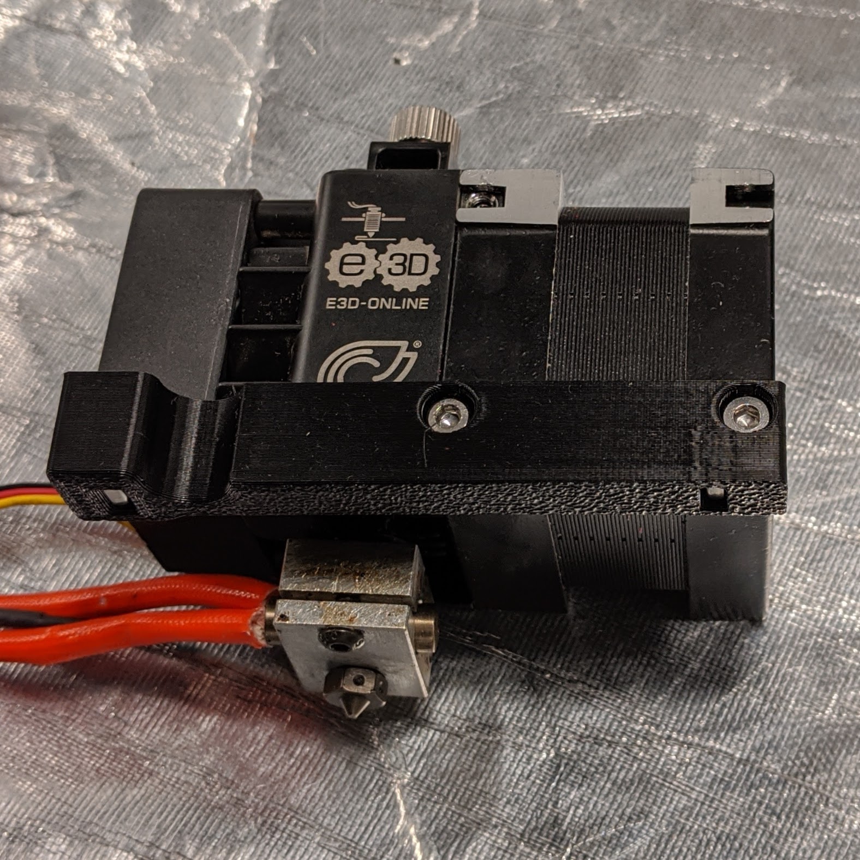
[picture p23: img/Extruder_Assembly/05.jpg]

---
### 05
* **Warning**, make sure you use the most recent vesrsion of the Undercarriage Right, the old version used 6mm instead of 8mm!!!
* Insert 1x thin square nut into the hemera mounting hole and secure the undercarriage right with 2x 8mm bolts<br>  
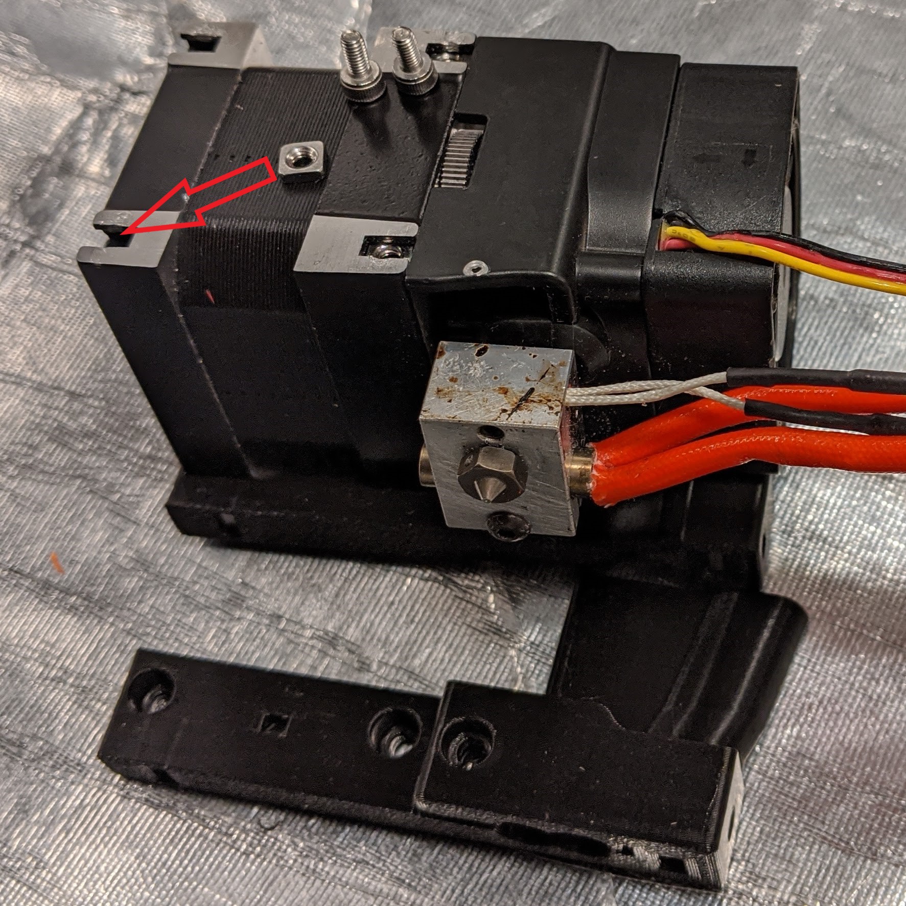
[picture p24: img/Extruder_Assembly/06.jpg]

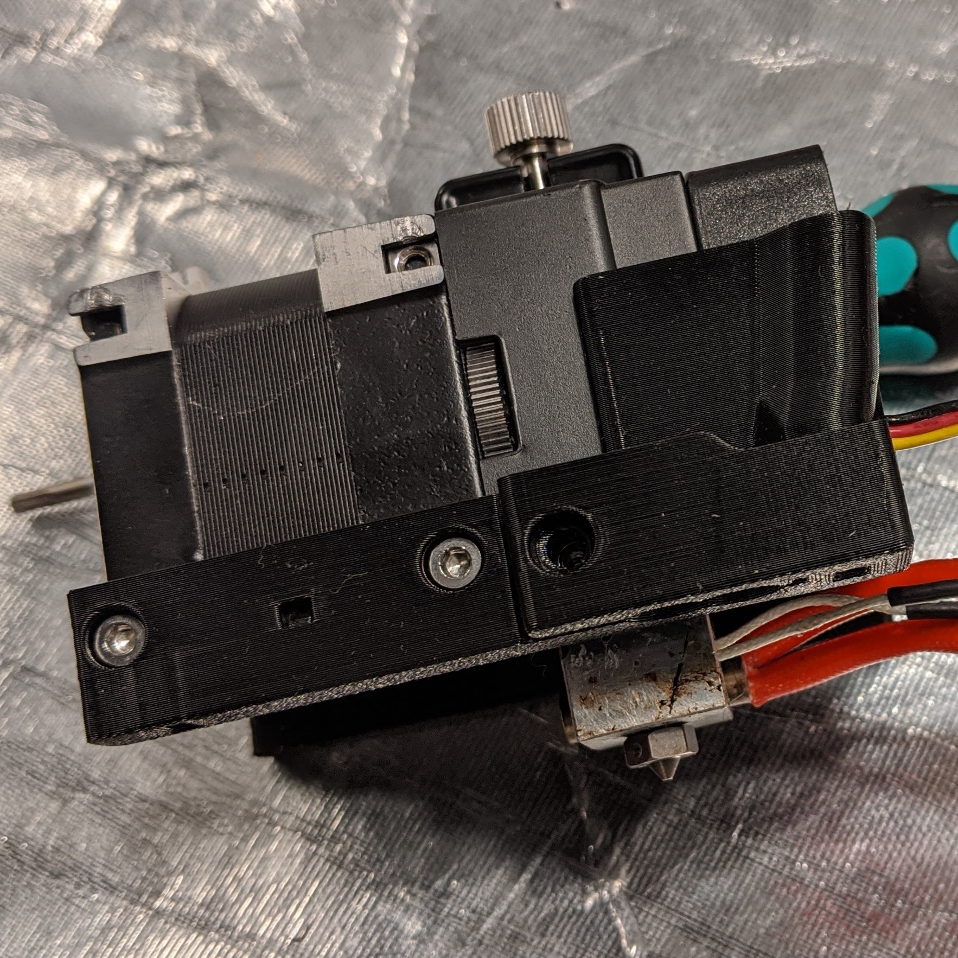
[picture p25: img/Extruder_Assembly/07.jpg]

---
### 06
* Insert the PINDA probe and secure in place with 1x 10mm bolt, **Do not overtight, just enough to prevent the PINDA rotating by hand**
* Use the front(motor side) hole for MK3/MK2.5 and the rear(fan side) hole for MK2 only
* **Do not squish the cable** behind the probe as pictured, it should sit just above<br>  
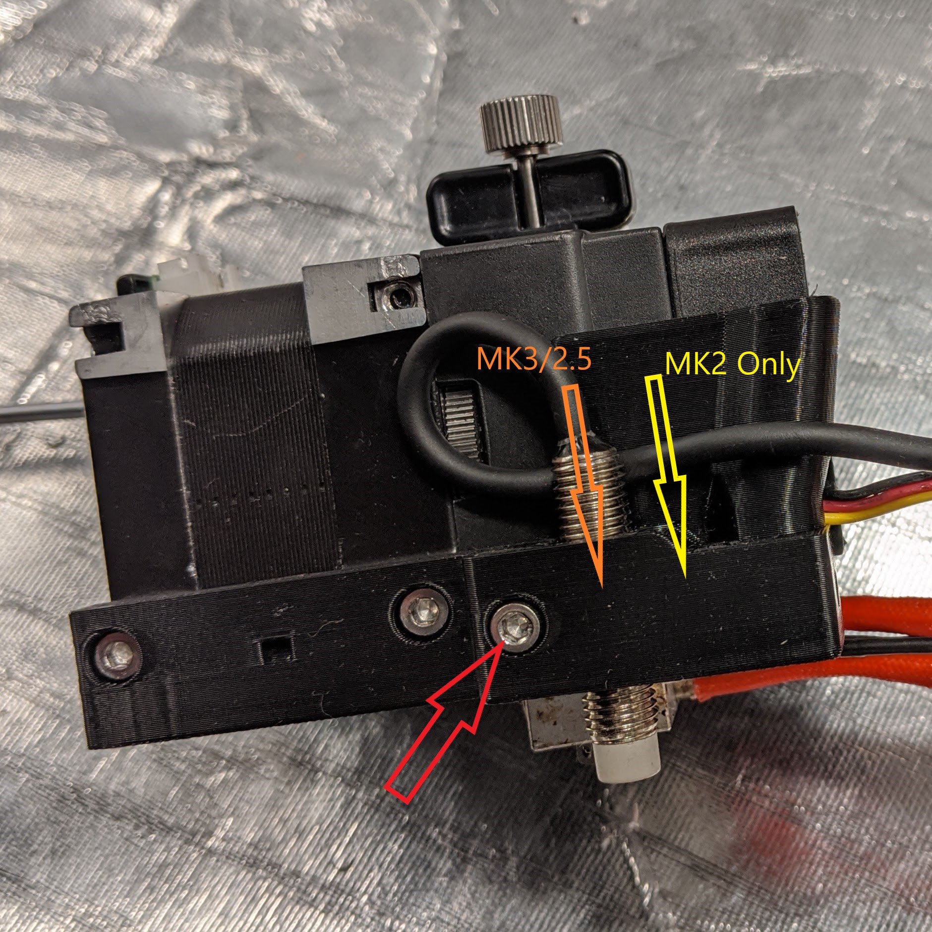
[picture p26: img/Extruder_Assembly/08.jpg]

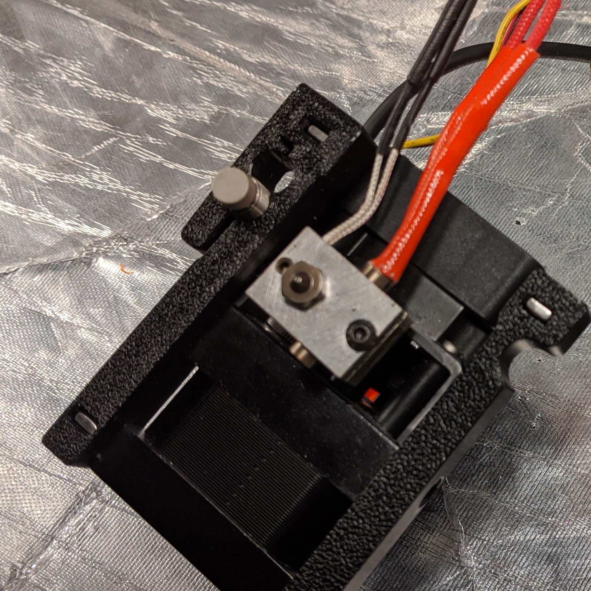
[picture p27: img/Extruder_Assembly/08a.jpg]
08a

---
### 07
* Take extra care here not to damage the thermistor or heater cartridge by yanking on the cables
* Get the undercarriage back part and 2x 14mm bolts<br>  
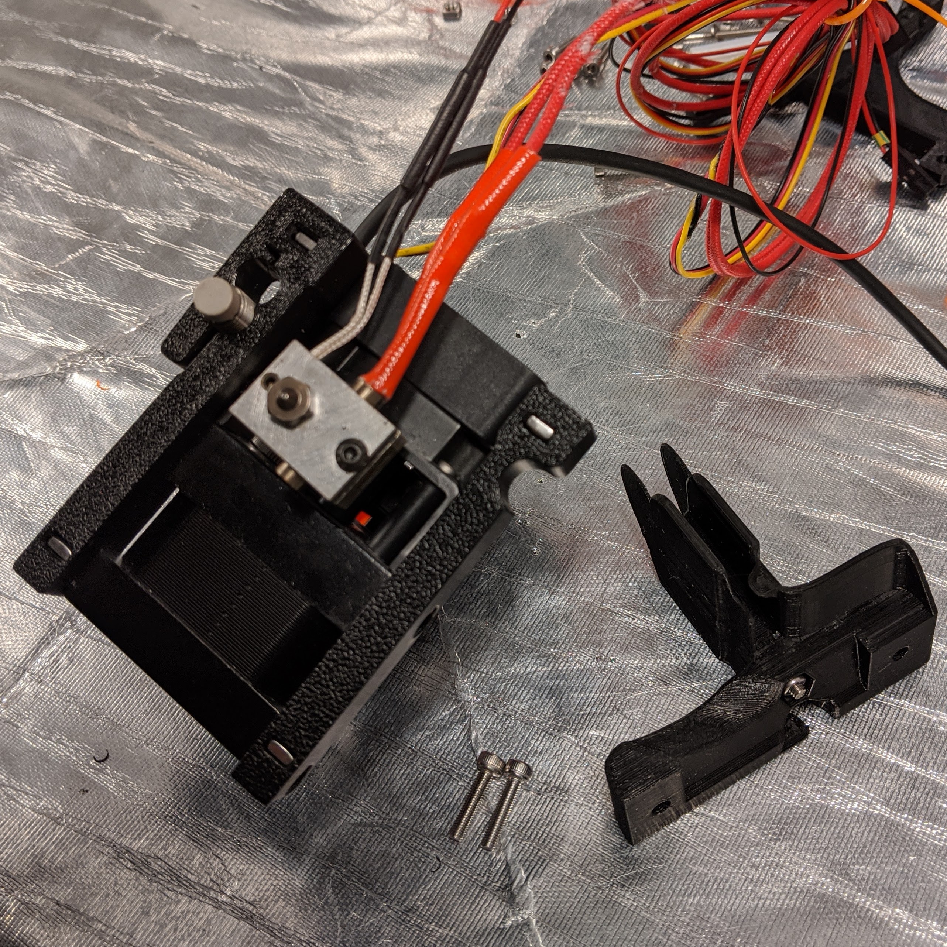
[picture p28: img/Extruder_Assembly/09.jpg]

---
### 08
* Carefully feed the thermistor cables as pictured<br>  
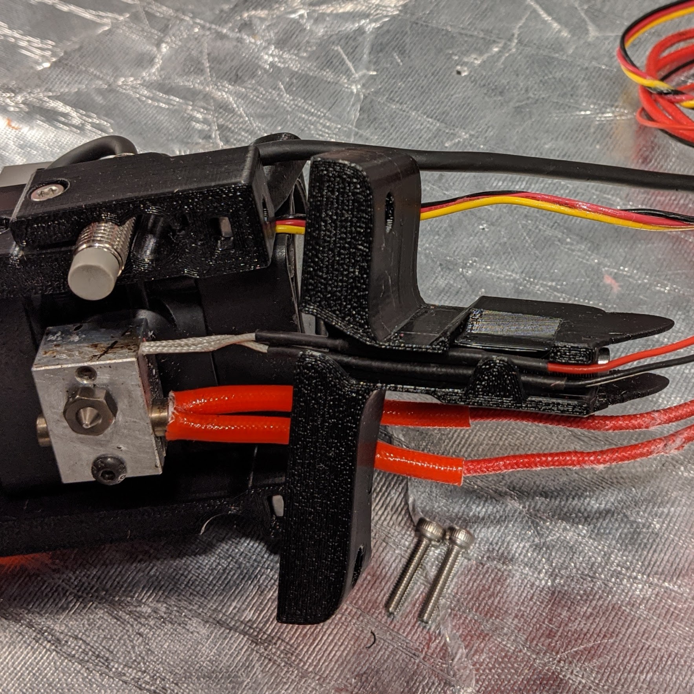
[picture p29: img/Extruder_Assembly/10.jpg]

---
### 09
* Carefully feed the heater cartridge cables as pictured
* It make take some gentle coercing to get them to sit correctly
* The undercarriage back should already be close to final position before securing in place with 2x 14mm bolt
* If the undercarriage back is not close, gently pull the cables through one by one, bit by bit taking particular care not to yank the cables<br>  
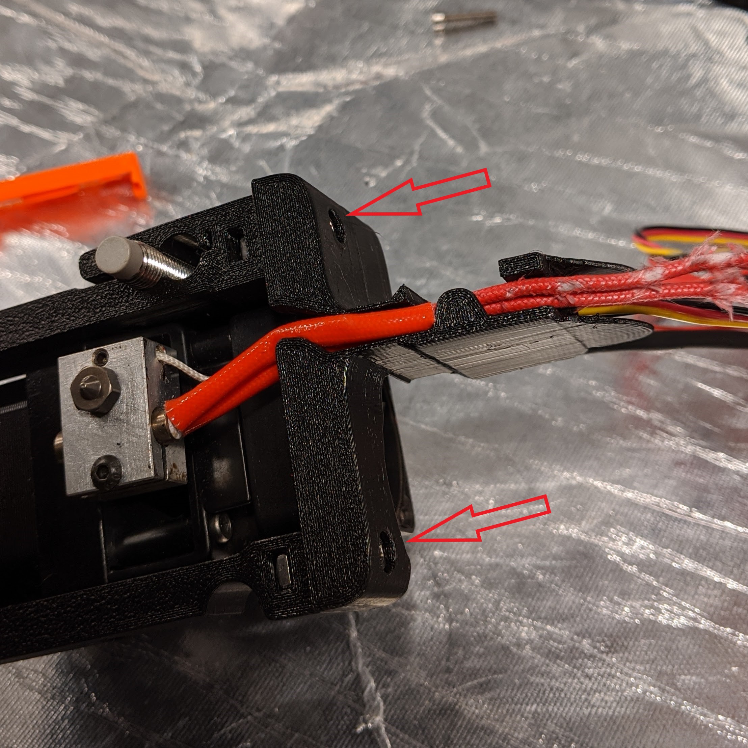
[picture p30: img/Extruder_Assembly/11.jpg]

---
[Previous](05_Filament_Sensor.md) | [Next](07_Extruder.md)

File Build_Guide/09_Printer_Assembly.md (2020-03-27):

[Previous](07_Extruder.md)   
---
# Extruder
### #hemeraodyssey
---
# Parts  
|Quantity|Size|Type|
|---:|:---:|:---:|
|1|[**HemeraOdyssey-X_Carriage_Belt_Tensioner_Left.stl**](../HemeraOdyssey_STLs_BETA/HemeraOdyssey-X_Carriage_Belt_Tensioner_Left.stl)|Printed Part|
|1|[**HemeraOdyssey-X_Carriage_Belt_Tensioner_Right.stl**](../HemeraOdyssey_STLs_BETA/HemeraOdyssey-X_Carriage_Belt_Tensioner_Right.stl)|Printed Part|
|1|[**HemeraOdyssey-Z_Top_Left_7mm.stl**](../HemeraOdyssey_STLs_BETA/HemeraOdyssey-Z_Top_Left_7mm.stl)|Printed Part (MK3S Only)|
|1|[**HemeraOdyssey-Z_Top_Right_7mm.stl**](../HemeraOdyssey_STLs_BETA/HemeraOdyssey-Z_Top_Right_7mm.stl)|Printed Part (MK3S Only)|
||mm|M3|
---
### 01
* <br>  
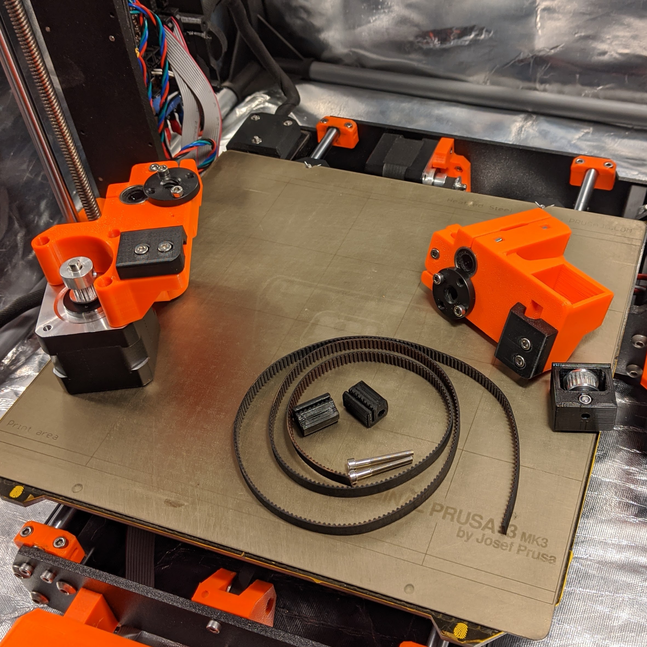
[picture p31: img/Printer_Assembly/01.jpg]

---
### 02
* <br>  
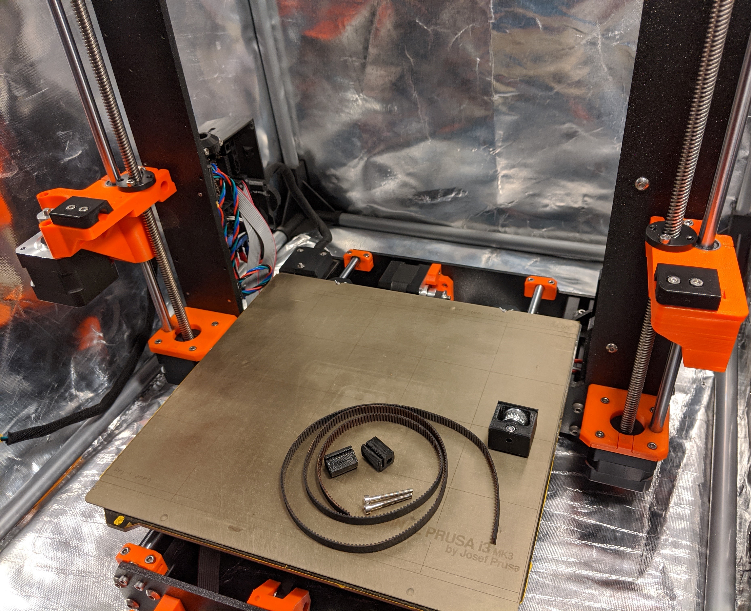
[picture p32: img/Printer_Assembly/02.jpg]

---
### 03
* MK3S Only
* Use 4x 12mm bolts to secure the Z Tops<br> 
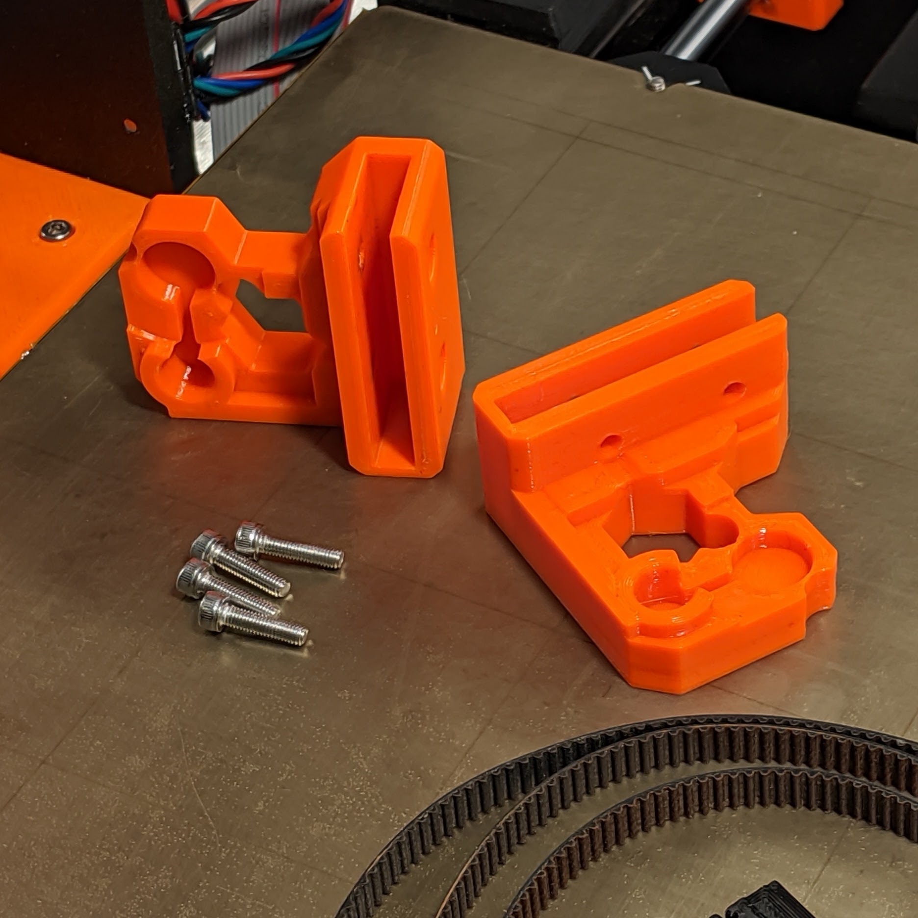
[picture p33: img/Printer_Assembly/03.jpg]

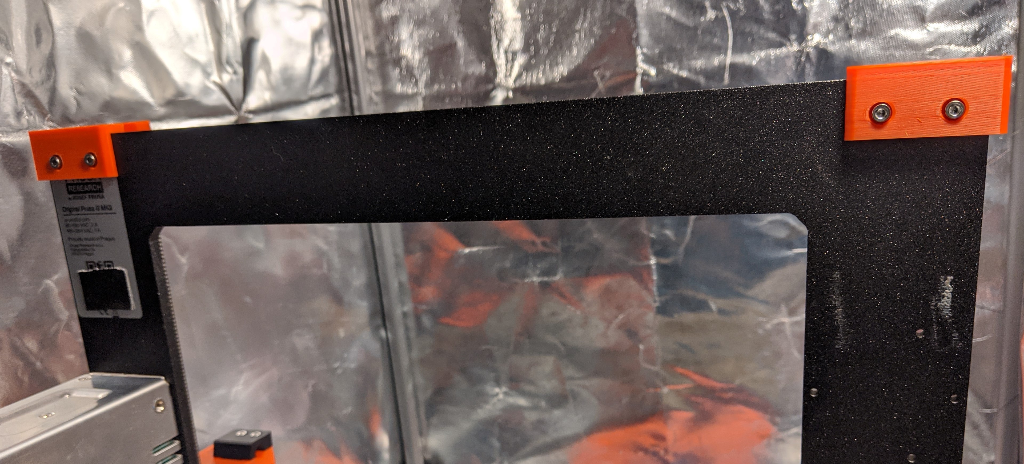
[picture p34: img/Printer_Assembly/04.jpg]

---
### 04
* <br>  
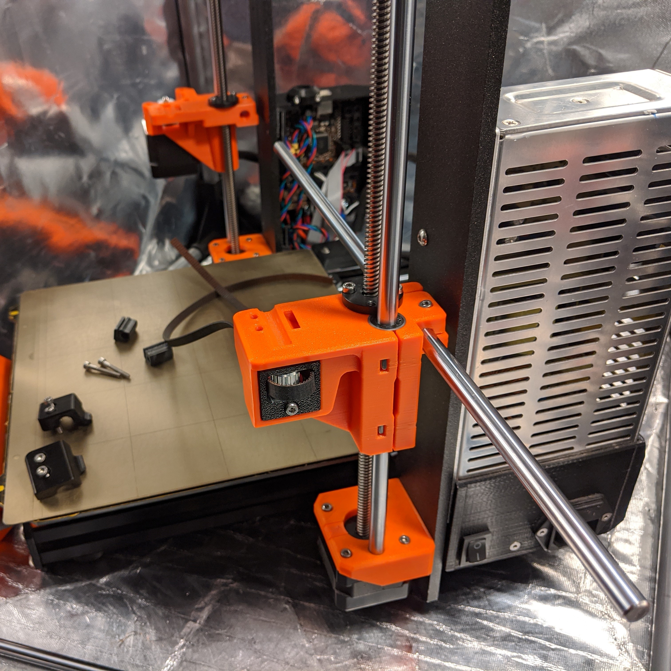
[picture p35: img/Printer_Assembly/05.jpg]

---
### 05
* <br>  
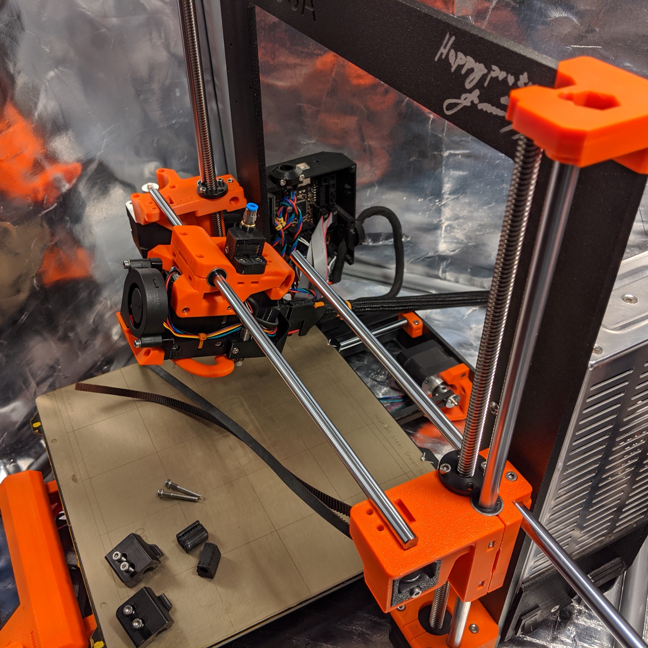
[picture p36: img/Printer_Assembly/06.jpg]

---
### 06
* <br>  
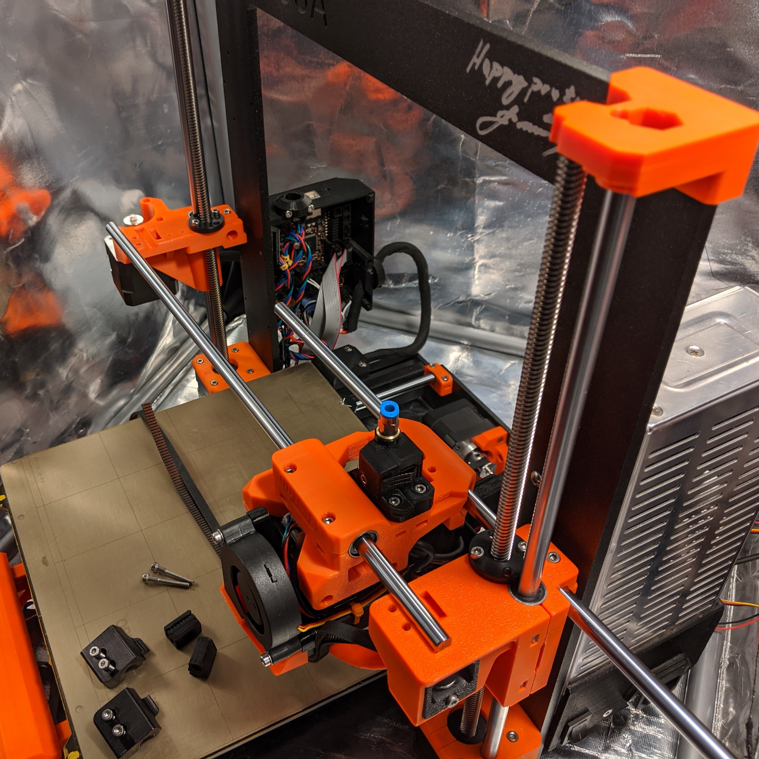
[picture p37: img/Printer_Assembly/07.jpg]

---
### 07
* <br>  

---
### 08
* <br>  
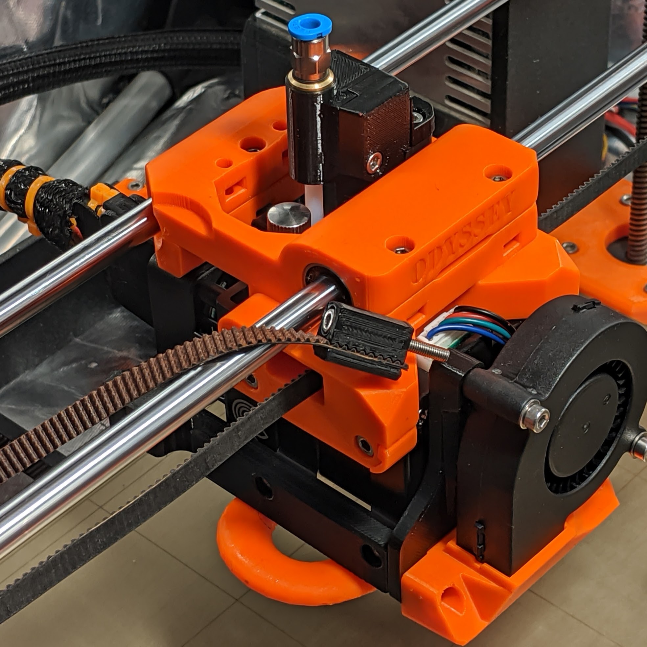
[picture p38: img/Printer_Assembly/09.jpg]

---
### 09
* Use 1x 25mm bolt to secure the belt clamp
* Fully tighten the bolt, this is **not** adjustable<br>  
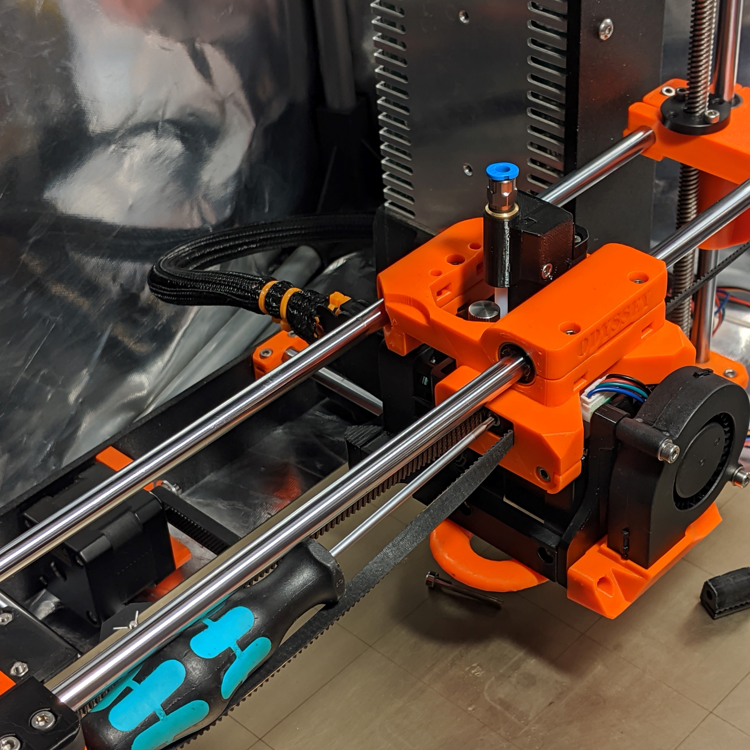
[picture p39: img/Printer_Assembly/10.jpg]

---
### 10
## Belt Tensioner  
* Use 1x 25mm bolt to secure the belt clamp, adjust belt position as needed before tightening the bolt
* There is only 5mm travel, so ensure the belt is taut and not protruding the x carriage before tensioning the belt<br>  
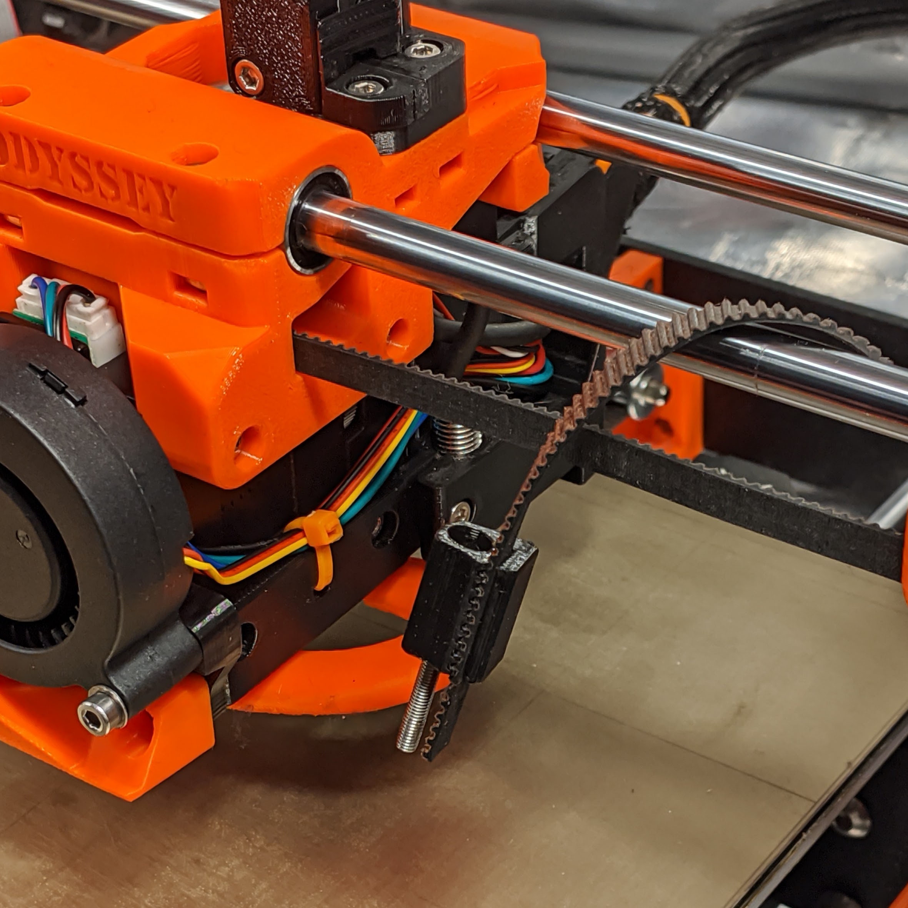
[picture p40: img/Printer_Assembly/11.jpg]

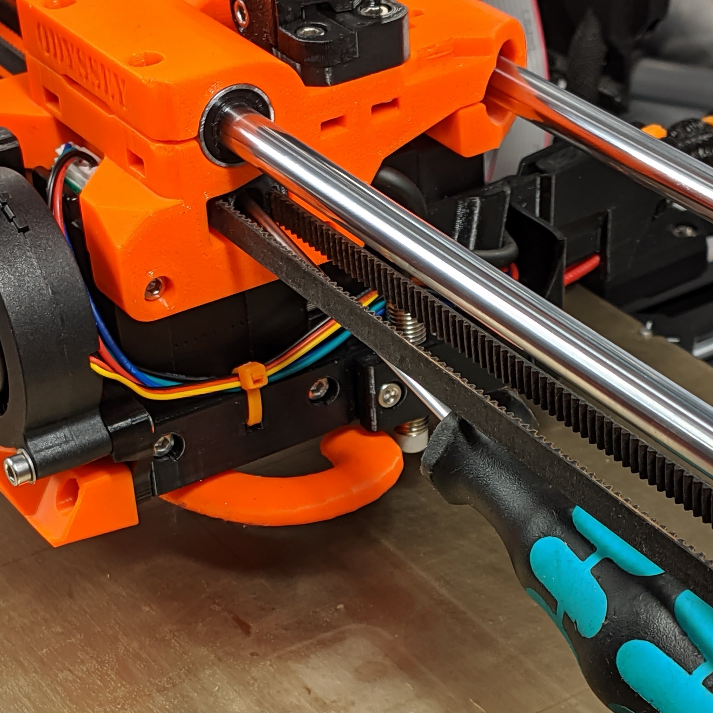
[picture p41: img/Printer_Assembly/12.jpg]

* Should looks like this after tensioning
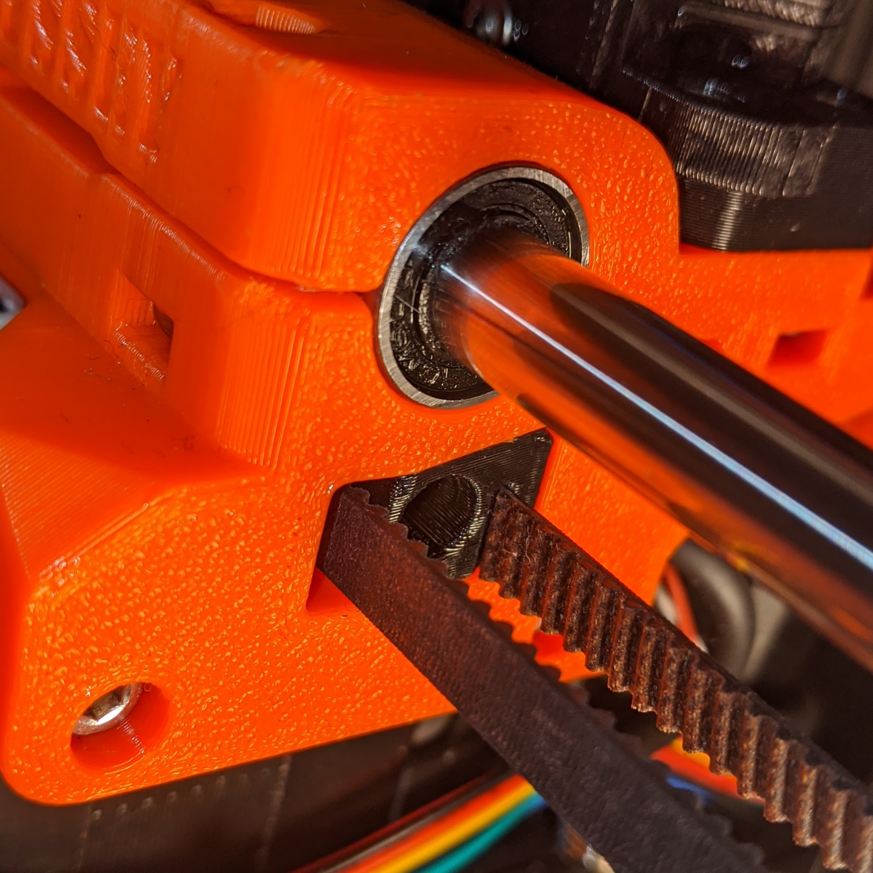
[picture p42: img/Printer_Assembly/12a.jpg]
12a

---
### 11
* This is the Idler adjuster (**NOT** a belt tensioner). It is used to align the belt.
* Fine adjustments are required
* Looking from this angle, move the x carriage back and forth
* If the belt sits low, then tighten the screw
* If the belt sits high, then losen the screw
* It is normal for the belt to travel slightly up and down, especially on the stock Prusa idelr
* This may require adjusting the motor drive gear up or down to get perfect
* I recommend getting a Gates idler due to the dual bearing making it easier to align<br>  
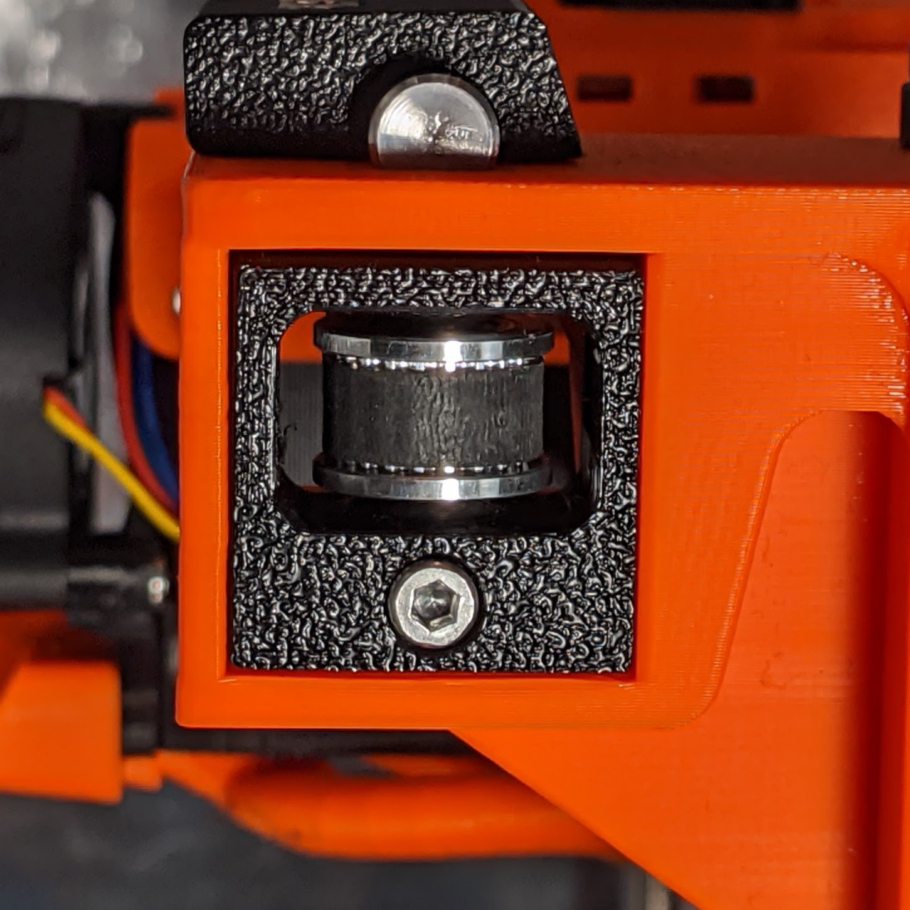
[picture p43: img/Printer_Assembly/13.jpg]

---
### 12
* <br>  
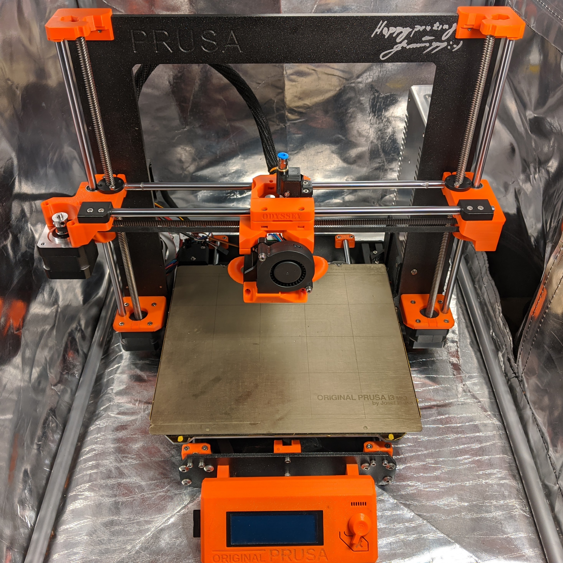
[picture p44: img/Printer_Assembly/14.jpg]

---
[Previous](07_Extruder.md)

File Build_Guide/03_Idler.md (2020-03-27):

[Previous](02_Part_Right.md) | [Next](04_X_Carriage.md)  
---
# Idler
### #hemeraodyssey
---
# Parts Stock
|Quantity|Size|Type|
|---:|:---:|:---:|
|1|[**HemeraOdyssey-Idler_Housing_Prusa_20T_3mmID.stl**](../HemeraOdyssey_STLs_BETA/HemeraOdyssey-Idler_Housing_Prusa_20T_3mmID.stl)|Printed Part|
|1|[**HemeraOdyssey-Idler_Housing_Prusa_20T_3mmID_Spacer_Top.stl**](../HemeraOdyssey_STLs_BETA/HemeraOdyssey-Idler_Housing_Prusa_20T_3mmID_Spacer_Top.stl)|Printed Part|
|1|[**HemeraOdyssey-Idler_Housing_Prusa_20T_3mmID_Spacer_Bottom.stl**](../HemeraOdyssey_STLs_BETA/HemeraOdyssey-Idler_Housing_Prusa_20T_3mmID_Spacer_Bottom.stl)|Printed Part|
|2|14mm|M3 Bolt|
|1|M3|Hex Nylon Lock Nut|
|1|Smooth T20|Prusa Idler|
---
### 01
* Gather the parts<br>  
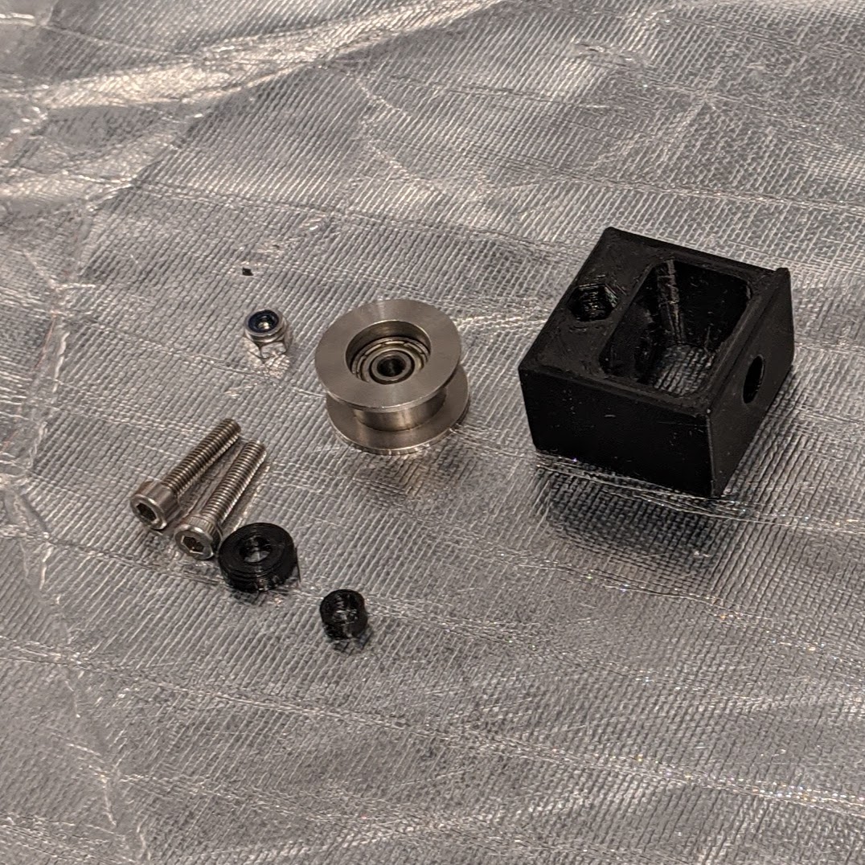
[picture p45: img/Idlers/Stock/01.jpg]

---
### 02
* Place the Spacer_Bottom in the large hole<br>  
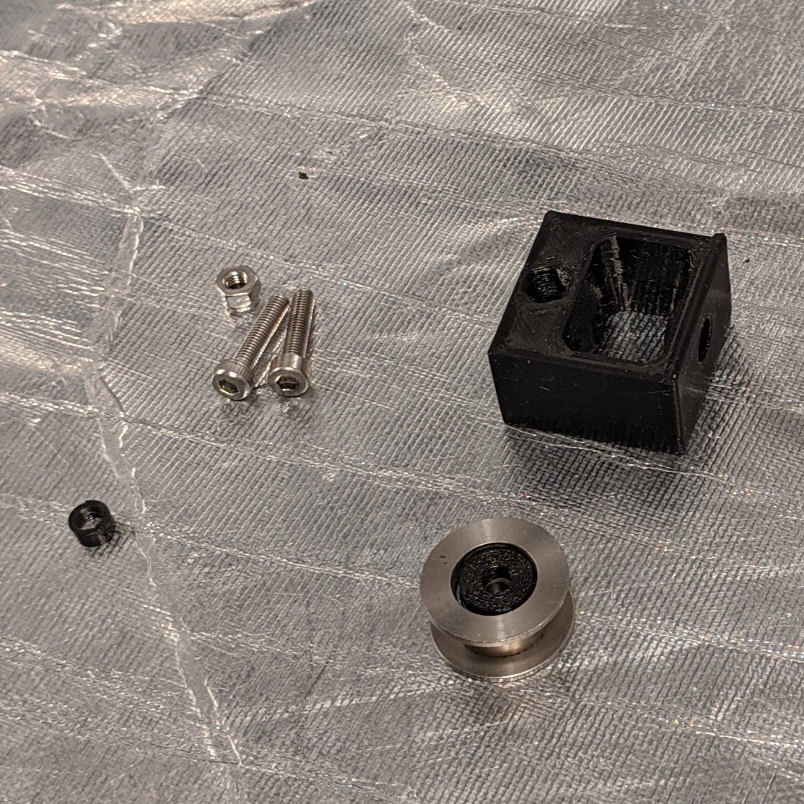
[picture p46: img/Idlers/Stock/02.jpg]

---
### 03
* Place the Spacer_Top in the small hole<br>  
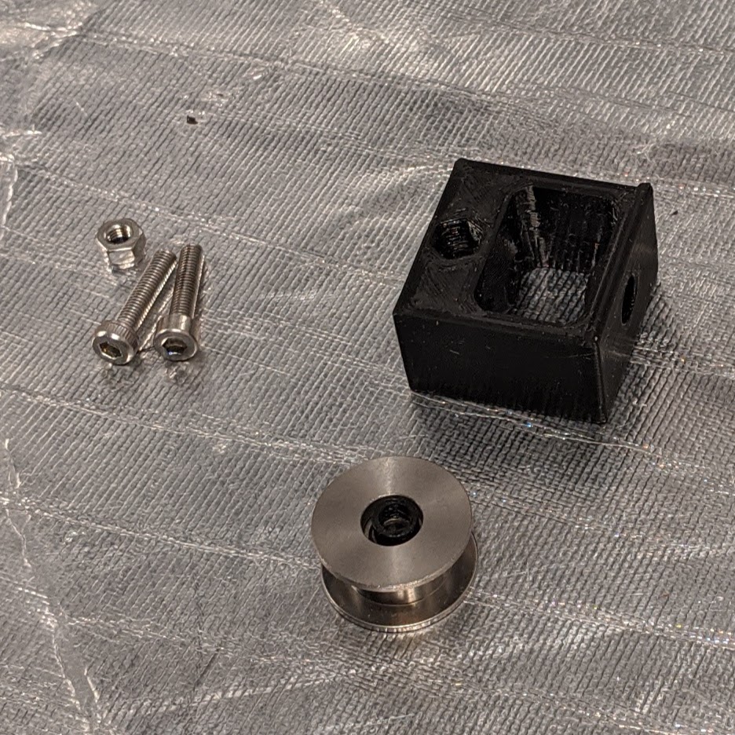
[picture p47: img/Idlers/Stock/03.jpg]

---
### 04
* Insert the assembled idler into the idler housing
* Secure the idler with 1 14mm bolt encuring not to overtighten. This is going into plastic so take it slow<br>  
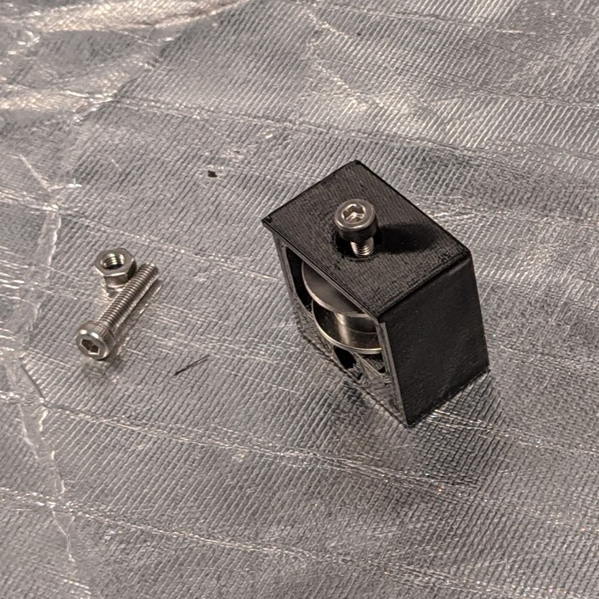
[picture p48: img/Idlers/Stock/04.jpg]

---
### 05
* Puncture the adjuster hole due to bridging support<br>  
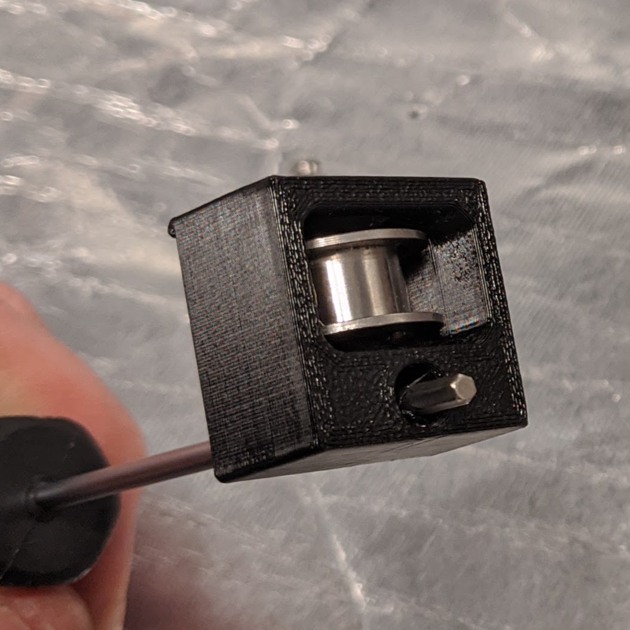
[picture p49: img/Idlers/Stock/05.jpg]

---
### 06
* Insert the Nylon Lock Nut and secure using 1 14mm bolt, then unscrew until bolt end is flush.<br>  
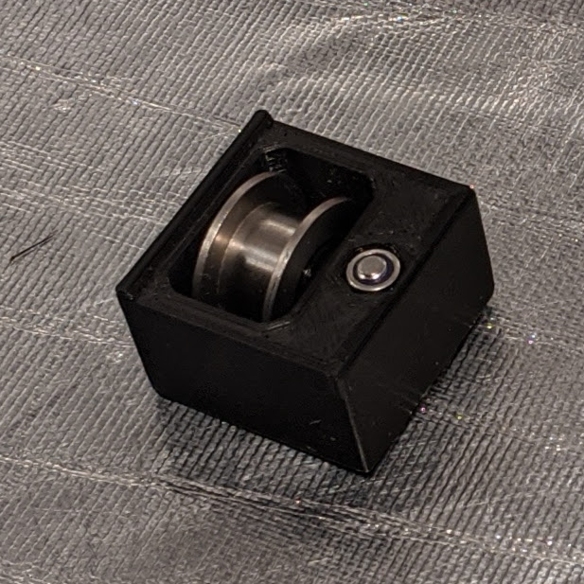
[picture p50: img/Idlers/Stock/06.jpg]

---
### 07
# Parts Gates
|Quantity|Size|Type|
|---:|:---:|:---:|
|1|[**HemeraOdyssey-Idler_Housing_Gates_20T_5mmID.stl**](../HemeraOdyssey_STLs_BETA/HemeraOdyssey-Idler_Housing_Gates_20T_5mmID.stl)|Printed Part|
|1|14mm-15.8mm|4.95mm OD Dowel for Gates Idler|
|1|14mm|M3 Bolt|
|1|M3|Nylon Lock Nut|
|1|Toothed T20|Gates Idler|
---
### 08
* Insert the Gates idler and secure in place using the dowel<br>  
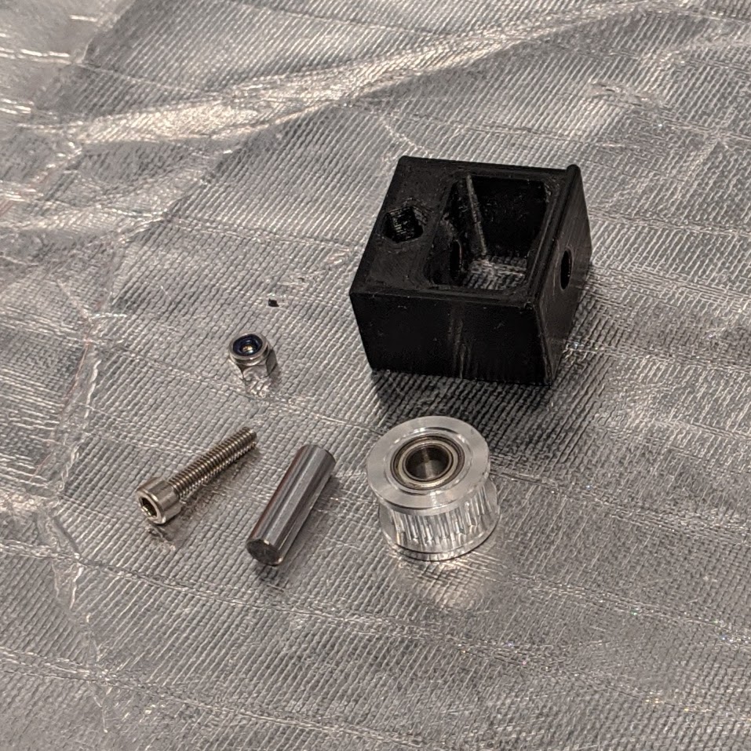
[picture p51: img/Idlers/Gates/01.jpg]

---
### 09
* Puncture the adjuster hole due to bridging support<br>  
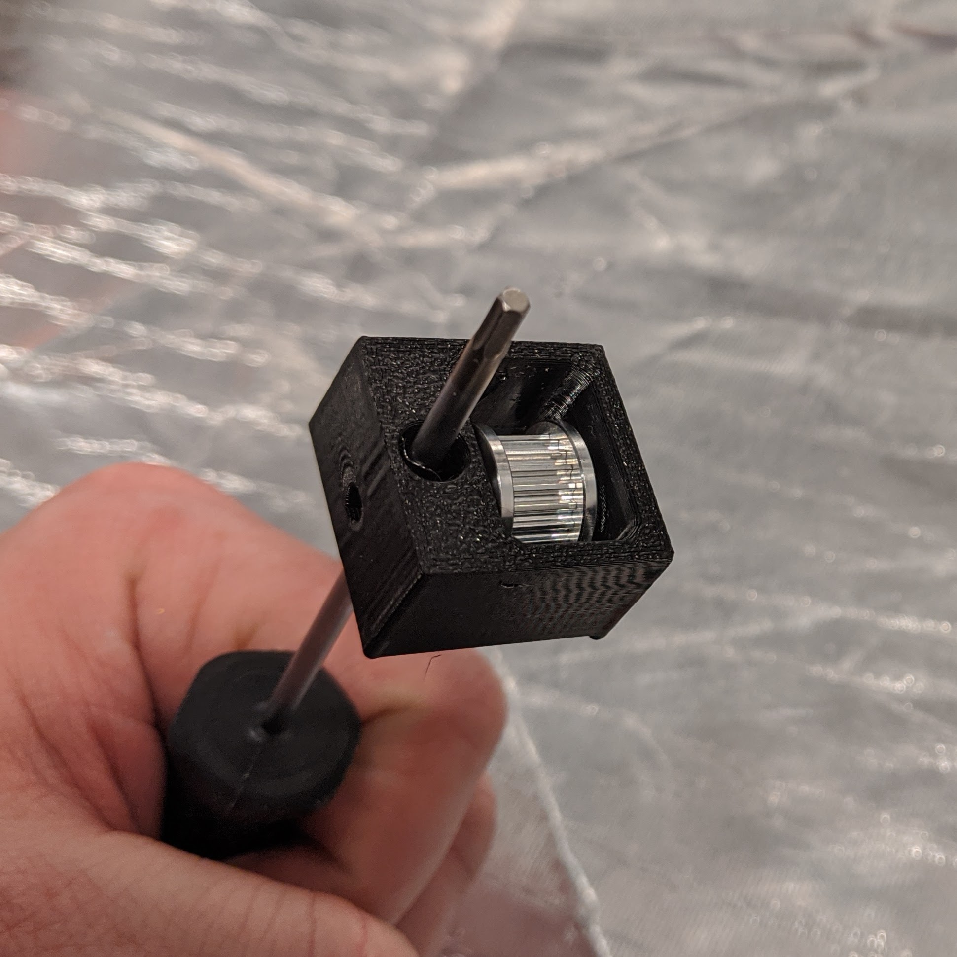
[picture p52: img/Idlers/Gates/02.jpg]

---
### 10
* Insert the Nylon Lock Nut and secure using 1 14mm bolt, then unscrew until bolt end is flush. (Not like the picture, will update it soon)<br>  
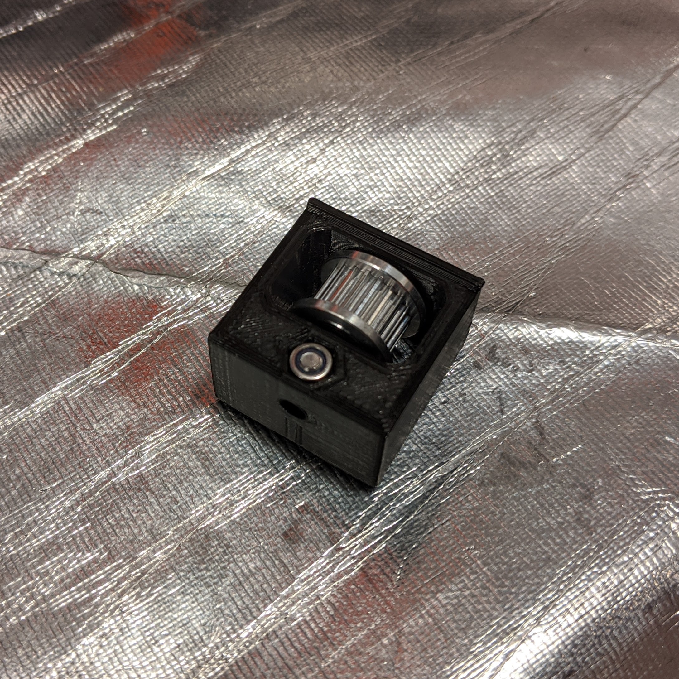
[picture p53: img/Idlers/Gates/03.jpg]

---
[Previous](02_Part_Right.md) | [Next](04_X_Carriage.md)

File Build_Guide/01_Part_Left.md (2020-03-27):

[Previous](00_First.md) | [Next](02_Part_Right.md)  
---
# Part Left  
### #hemeraodyssey
---
# Parts  
|Quantity|Size|Type|
|---:|:---:|:---:|
|1|[**HemeraOdyssey-Part_Left_Motor.stl**](../HemeraOdyssey_STLs_BETA/HemeraOdyssey-Part_Left_Motor.stl)|Printed Part|
|1|[**HemeraOdyssey-Part_Left_Front_Rod_Clamp.stl**](../HemeraOdyssey_STLs_BETA/HemeraOdyssey-Part_Left_Front_Rod_Clamp.stl)|Printed Part|
|2|10mm|M3(Not needed yet)|
|5|14mm|M3 Bolt|
|5|18mm|M3 Bolt|
|5|M3|Hex Nut|
|2|M3|Square Nut|
|1|POM Trapezoidal Nut|T8|
|2|LM8UU|Bearing|  
---
### 01
* Puncture the back rod clamp hole using the M3 hex driver due to the bridging support  
* Insert a smooth rod into the back clamp to break the support then clear out the support material carefully using a knife or thin metal ruler.  <br>  
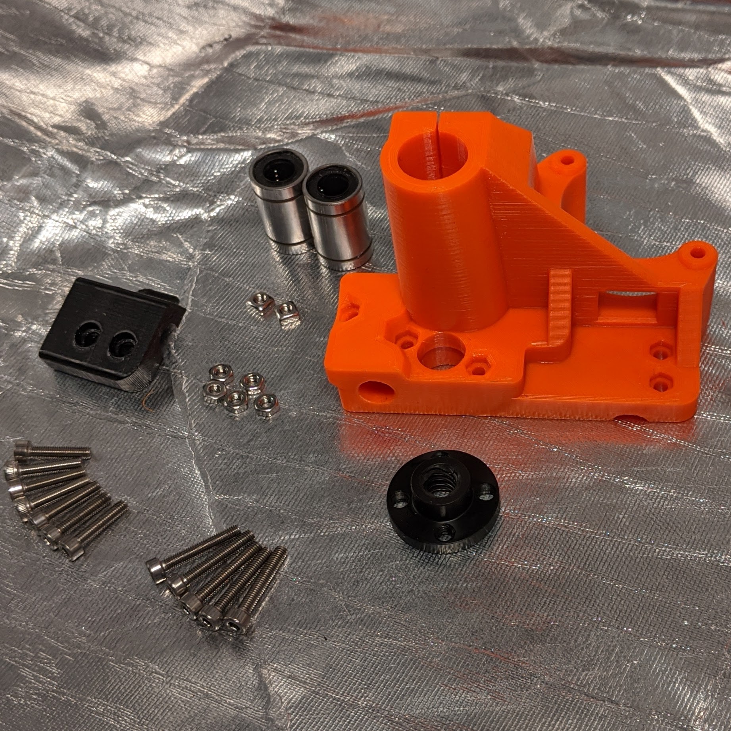
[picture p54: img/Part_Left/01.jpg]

---
### 02
* Insert all 5x hex nuts using a 14mm bolt from the rear<br>  
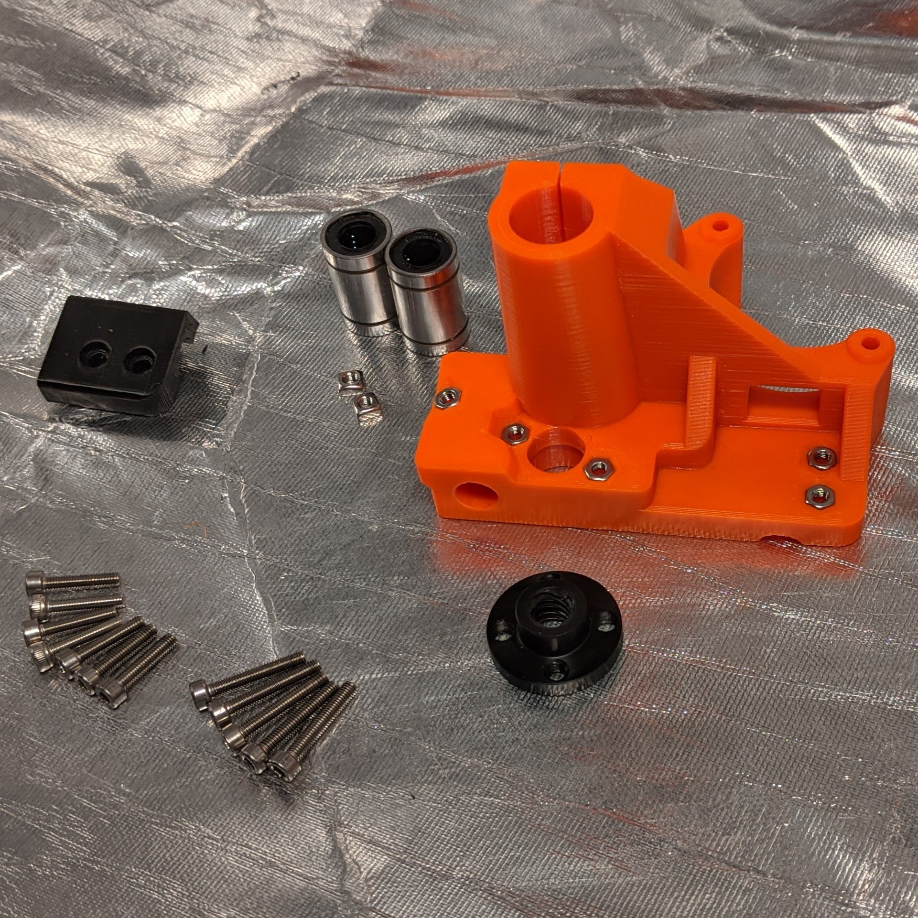
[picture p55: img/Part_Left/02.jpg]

---
### 03
* Insert both LM8UU bearings in X configuration (looking down from front & above) for both<br>  


---
### 04
* Insert 2 square nuts  
* Insert 2 14mm bolts to secure, don't over tighten<br>  

---
### 05
* Loosely fit the front clamp part with 2x 14mm bolt and loosely insert 1x 14mm bolt in the rear clamp<br>  

---
### 06
* Loosely fit the POM Trapezoidal Nut using 2x 18mm bolts<br>  

---
### 07
* Puncture the 3x motor holes using the M3 hex driver due to the bridging support<br>  

---
### 08
* Secure the motor with 3x 18mm bolts
* For MK2/MK2.5 secure the endstop microswitch using 2x M2 12mm<br>  

---
[Previous](00_First.md) | [Next](02_Part_Right.md)

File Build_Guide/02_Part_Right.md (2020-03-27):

[Previous](01_Part_Left.md) | [Next](03_Idler.md)  
---
# Part Right
### #hemeraodyssey
---
# Parts  
|Quantity|Size|Type|
|---:|:---:|:---:|
|1|[**HemeraOdyssey-Part_Right_Idler.stl**](../HemeraOdyssey_STLs_BETA/HemeraOdyssey-Part_Right_Idler.stl)|Printed Part|
|1|[**HemeraOdyssey-Part_Right_Front_Rod_Clamp.stl**](../HemeraOdyssey_STLs_BETA/HemeraOdyssey-Part_Right_Front_Rod_Clamp.stl)|Printed Part|
|5|14mm|M3 Bolt|
|2|18mm|M3 Bolt|
|5|M3|Hex Nut|
|2|M3|Square Nut|
|1|T8|POM Trapezoidal Nut|
|2|LM8UU|Bearing|  
---
### 01
* Snap off brim support
* Puncture the back rod clamp hole using the M3 hex driver due to bridging support <br>  

---
### 02
* Insert all 5 hex nuts using a 14mm bolt from the rear<br>  

---
### 03
* Insert both LM8UU bearings in X configuration (looking down from front & above) for both<br>  


---
### 04
* Insert 2x square nuts  
* Insert 2x 14mm bolts to secure, don't over tighten<br>  

---
### 05
* Loosely fit the POM Trapezoidal Nut using 2x 18mm bolts<br>  

---
### 06
* Loosely fit the front clamp part with 2x 14mm bolt and loosely insert 1x 14mm bolt in the rear clamp<br>  

---
[Previous](01_Part_Left.md) | [Next](03_Idler.md)

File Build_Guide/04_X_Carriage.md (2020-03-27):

[Previous](03_Idler.md) | [Next](05_Filament_Sensor.md)  
---
# X Carriage
### #hemeraodyssey
---
# Parts  
|Quantity|Size|Type|
|---:|:---:|:---:|
|1|[**HemeraOdyssey-X_Carriage.stl**](../HemeraOdyssey_STLs_BETA/HemeraOdyssey-X_Carriage.stl)|Printed Part|
|2|M3|Hex Nylon Lock Nut|
|2|14mm|M3 Bolt|
|3|M3|Square Nut|
|3|LM8UU|Bearing| 
---
### 01
* Puncture the clamp holes and belt tensioner hole using the M3 hex driver due to bridging support
* Nylon Lock Nut orientation<br>  

---
### 02
* Push down then back into the hole. Using a bolt in the tensioner holes can help engage the lock nut into place<br>  

---
### 03
* Do the same for the other side<br>   

---
### 03
* Insert both front LM8UU bearings in X configuration for both, so two rows of bearing sit on top when mounted<br>  
 

---
### 04
* Insert rear LM8UU bearings in X configuratio, so two rows of bearing sit on top when mounted<br>  

---
### 05
* Insert 2 square nuts  
* Insert 2 14mm bolts to secure, don't over tighten<br>  

---
### 06
* Insert 1 square nuts<br>  

---
### 07
* Insert 1 14mm bolts to secure, don't over tighten<br>   

---
[Previous](03_Idler.md) | [Next](05_Filament_Sensor.md)

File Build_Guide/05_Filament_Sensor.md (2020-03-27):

[Previous](04_X_Carriage.md) | [Next](06_Undercarriage.md)  
---
# Filament Sensor
### #hemeraodyssey
---
# Parts IR Sensor
|Quantity|Size|Type|
|---:|:---:|:---:|
|1|[**HemeraOdyssey-Filament_Sensor_IR_Housing.stl**](../HemeraOdyssey_STLs_BETA/HemeraOdyssey-Filament_Sensor_IR_Housing.stl)|Printed Part|
|1|[**HemeraOdyssey-Filament_Sensor_IR_Cover.stl**](../HemeraOdyssey_STLs_BETA/HemeraOdyssey-Filament_Sensor_IR_Cover.stl)|Printed Part|
|1|[**HemeraOdyssey-Filament_Sensor_IR_Trigger.stl**](../HemeraOdyssey_STLs_BETA/HemeraOdyssey-Filament_Sensor_IR_Trigger.stl)|Printed Part|
|1|[**HemeraOdyssey-Filament_Sensor_IR_Spring.stl**](../HemeraOdyssey_STLs_BETA/HemeraOdyssey-Filament_Sensor_IR_Spring.stl)|Printed Part|
|2|14mm|M3 Bolt|
|1|10mm|M3 Bolt|
|1|7mm|Ball Bearing|
|1||IR filament sensor|
---
### 01

---
### 02
* Insert the ball bearing into the housing or onto the trigger as pictured<br>  

---
### 03
* Insert the trigger into the housing with the flat edge facing outward<br>  

---
### 04
* Place the IR filament sensor into the side as pictures. This will prevent the trigger from falling out<br>  

---
### 05
* The cover alignment tab has a support structure that needs to be snapped off.
* Carefully place over the IR filament sensor, ensuring the alignment tab seats correctly and the cover sits flat against the housing
* Use the 10mm bolt to secure the cover in place<br>  


---
### 06
* Gently bend the end of the spring as pictured being careful not to overbend<br>  

---
### 07
# Parts Laser Sensor
|Quantity|Size|Type|
|---:|:---:|:---:|
|1|[**HemeraOdyssey-Filament_Sensor_Laser_Housing.stl**](../HemeraOdyssey_STLs_BETA/HemeraOdyssey-Filament_Sensor_Laser_Housing.stl)|Printed Part|
|1|[**HemeraOdyssey-Filament_Sensor_Laser_Lid.stl**](../HemeraOdyssey_STLs_BETA/HemeraOdyssey-Filament_Sensor_Laser_Lid.stl)|Printed Part|
|1|[**HemeraOdyssey-Filament_Sensor_Laser_Wahser.stl**](../HemeraOdyssey_STLs_BETA/HemeraOdyssey-Filament_Sensor_Laser_Wahser.stl)|Printed Part|
|2|14mm|M3 Bolt|
|3|10mm|M3 Bolt|
|1|11mm|PTFE Tube|
---
### 08

---
### 09
* Insert the Laser filament sensor
* Insert the 11mm PTFE tube
* Insert 1x 10mm bolt into the washer, making sure the bolt is free to move independently from the washer<br>  

---
### 10
* Secure the laser filament sensor using the washer bolt combo. Ensure the flat side of the washer aligns down. This is screwing into plastic so take it slow<br>  

---
### 11
* Insert 2x 14mm bolts into the back two holes<br>  

---
### 12
* Secure the lid using 2x 10mm bolts. They screw into plastic so take it slow<br>  

---
[Previous](04_X_Carriage.md) | [Next](06_Undercarriage.md)

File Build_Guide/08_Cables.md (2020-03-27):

[Previous](07_Extruder.md) | [Next](09_Printer_Assembly.md)  
---
# Cables
### #hemeraodyssey
---
# Parts  
|Quantity|Size|Type|
|---:|:---:|:---:|
|1|[**HemeraOdyssey-Undercarriage_Back_Cap.stl**](../HemeraOdyssey_STLs_BETA/HemeraOdyssey-Undercarriage_Back_Cap.stl)|Printed Part|
|1|3mm|Nylon Filament|
|6|Small|zip tie|
---
### 01
* Insert the 3mm nylon filament (cable support) into the pictured hole on the undercarraige back part
* Make sure it goes all the way in<br>  


---
### 02
* Guide the cables in this order through the upper gully on the undercarraige back part
1. Hemera fan cable
2. Filament sensor cable
3. Motor cable
4. Blower fan cable
5. PINDA probe cable<br>  

---
### 03
* Slide in the undercarriage back cap taking note of the arrow pointing towards the Hemera<br>  

---
### 04
* Take one zip tie under the nylon and around the upper cables<br>  
 
* Take one zip tie under the nylon and over the upper cables<br>  
 

* Tighten the zip tie using pliers (not crazy tight)<br>  

---
### 05
* Repeat the above with one other zip tie<br>  


---
### 06
* Take one zip tie over the nylon and around the lower cables<br>  

---
### 07
* Slide up towards the hemera and tighten by hand<br>  

---
### 08
* Take one zip tie over around all the cables<br>  

---
### 09
* Trim all the zip ties using snippers<br>  

---
### 10
* Feed the cables into the original sleve and secure in place with a couple zip ties, tightened by hand and trimmed<br>  

---
[Previous](07_Extruder.md) | [Next](09_Printer_Assembly.md)

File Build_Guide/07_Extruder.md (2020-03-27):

[Previous](06_Undercarriage.md) | [Next](08_Cables.md)  
---
# Extruder
### #hemeraodyssey
---
# Parts  
|Quantity|Size|Type|
|---:|:---:|:---:|
|1|[**HemeraOdyssey-X_Carriage.stl**](../HemeraOdyssey_STLs_BETA/HemeraOdyssey-X_Carriage.stl)|Printed Part|
|1|[**HemeraOdyssey-X_Carriage_Washer.stl**](../HemeraOdyssey_STLs_BETA/HemeraOdyssey-X_Carriage_Washer.stl)|Printed Part|
|1|[**HemeraOdyssey-Nozzle_Fang.stl**](../HemeraOdyssey_STLs_BETA/HemeraOdyssey-Nozzle_Fang.stl)|Printed Part|
|4|10mm|M3 Bolt|
|2|16mm|M3 Bolt|
|2|25mm|M3 Bolt|
|2|M3|Thin Square Nut (Hemera)|
|2|M3|Washer|
|1|43mm|PTFE Tube|
|1|Small|zip tie|
---
### 01
* Get the X carriage part + washer part, 4x 10mm bolts and 2x thin square nuts<br>  

---
### 02
* Place the printed washer part onto the X carriage as pictured<br>  

---
### 03
* Insert 2x thin square nuts into the mounting holes on the hemera and ensuring you don't tip them out
* If you find this difficult to achieve, you can leave them out until the next step<br>  

---
### 04
**NOTE: It is possible to place and remove the motor cable with the x carriage in place, but you may want to add it now**  
* Place the X carriage over the Hemera mounting holes as pictured
* Insert the 2x thin square nuts into the mounting slots if they have fallen out by this point<br>  

---
### 05
* Secure the X carriage to the hemera using 4x 10mm bolts, do *not* over tighten<br>  

---
### 06
* Get the nozzel fang, undercarriage fan mount, 2x 16mm bolt, 2x Hex Nylon Lock Nut and motor cable<br>  

---
### 07
* **Make sure the plastic sleeve is removed from the motor cable**
* Connect the motor cable and guide it to the back passing behind the pinda<br>  

---
### 08
* Insert 2x Hex Nylon Lock Nut onto the printed undercarriage fan mount. You can use a spare 10mm bolt to bed them
* Place the undercarriage fan mount against the nozzle fang and insert 2x 16mm bolts to hold it in place<br>  

---
### 09
* Secure the nozzle fang and undercarriage fan mount to the undercarriage assembly as pictured by tightening the 2x 16mm bolts<br>  

---
### 10
* Secure the 50mm blower fan using 2x 25mm bolt with 2x M3 washers
* Guide the fan cable the same way as the motor cable<br>  


---
### 11
* Secure the motor and fan cable to the undercarraige rigth part using a small zip tie<br>  


---
### 12
* Insert the 43mm PTFE tube into the hemera<br>  

---
## Laser Filament Sensor
* Attach the dupont connector to the sensor
* Feed the cable through the opening of the X Carriage down past the PINDA
* Place the cable in the slot on the underside of the sensor housing
* Locate the PTFE tube and isert into the sensor housing
* Secure the sensor housing in the corner as pictured, ensuring not to pinch the cable<br>  

 

---
## IR Filament Sensor
* Attach the dupont connector to the sensor
* Feed the cable through the opening of the X Carriage down past the PINDA
* Secure the sensor as pictured using 2x 14mm bolts<br>  

30a

---
[Previous](06_Undercarriage.md) | [Next](08_Cables.md)

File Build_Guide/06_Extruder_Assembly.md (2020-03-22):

[Previous](05_Filament_Sensor.md) | [Next](07_Printer_Assembly.md)  
### #hemeraodyssey
---
# Extruder
---
# Parts  
|Quantity|Size|Type|
|---:|:---:|:---:|
|1|[**HemeraOdyssey-Undercarriage_Left.stl**](../HemeraOdyssey_STLs_BETA/HemeraOdyssey-Undercarriage_Left.stl)|Printed Part|
|1|[**HemeraOdyssey-Undercarriage_Right.stl**](../HemeraOdyssey_STLs_BETA/HemeraOdyssey-Undercarriage_Right.stl)|Printed Part|
|1|[**HemeraOdyssey-Undercarriage_Back.stl**](../HemeraOdyssey_STLs_BETA/HemeraOdyssey-Undercarriage_Back.stl)|Printed Part|
|1|[**HemeraOdyssey-Undercarriage_Back_Cap.stl**](../HemeraOdyssey_STLs_BETA/HemeraOdyssey-Undercarriage_Back_Cap.stl)|Printed Part|
|1|[**HemeraOdyssey-X_Carriage.stl**](../HemeraOdyssey_STLs_BETA/HemeraOdyssey-X_Carriage.stl)|Printed Part|
|1|[**HemeraOdyssey-X_Carriage_Washer.stl**](../HemeraOdyssey_STLs_BETA/HemeraOdyssey-X_Carriage_Washer.stl)|Printed Part|
|1|[**HemeraOdyssey-Nozzle_Fang.stl**](../HemeraOdyssey_STLs_BETA/HemeraOdyssey-Nozzle_Fang.stl)|Printed Part|
|5|10mm|M3 Bolt|
|4|14mm|M3 Bolt|
|4|25mm|M3 Bolt|
|1|40mm|M3 Bolt|
|5|M3|Square Nut|
|4|M3|Thin Square Nut (Hemera)|
|1|M3|Hex Nylon Lock Nut|
|2|M3|Washer|
|4|6mm|M3 Bolt (Hemera)|
|1|43mm|PTFE Tube|
|1|3mm|Nylon Filament|
---
* Ensure the Hemera is assembled according to [E3D build guide](https://e3d-online.dozuki.com/c/Hemera_Assembly_Guides)
* Do **not** use the stock Noctua fan, you will only get jamms
* The only recommended fan is the one provided with the Hemera, see [here](00_First.md) for more details<br>  

---
* Insert 1x 40mm bolt into the undercarriage back and secure with a hex nylon lock nut, tighten completely
* This provides strength<br>  

---
* The undercarriage left requires 2x square nuts
* The undercarriage right requires 3x square nuts<br>  
02a
02b
02c
---
* Insert a thin square nut into the hemera mounting hole and secure the undercarriage left with 2x 6mm bolts<br>  
 

---
* Insert a thin square nut into the hemera mounting hole and secure the undercarriage right with 2x 6mm bolts<br>  


---
* Insert the PINDA probe and secure in place with 1x 10mm bolt
* Use the front(motor side) hole for MK3/MK2.5 and the rear(fan side) hole for MK2 only<br>  

08a
---
* Take extra care here not to damage the thermistor or heater cartridge by yanking on the cables
* Get the undercarriage back part and 2x 14mm bolts<br>  

---
* First feed the thermistor cables as pictured<br>  

---
* Second carefully feed the heater cartridge cables as pictured
* It make take some gentle coercing to get them to sit correctly
* The undercarriage back should already be close to final position before securing in place with 2x 14mm bolt
* If the undercarriage back is not close, gently pull the cables through one by one, bit by bit taking particular care not to yank the cables<br>  

---
* Get the X carriage part + washer part, 4x 10mm bolts and 2x thin square nuts<br>  

---
* Place the washer part onto the X carriage as pictured<br>  

---
* Insert 2x thin square nuts into the mounting holes on the hemera and ensuring you don't tip them out
* If you find this difficult to achieve, you can leave them out until the next step<br>  

---
* Place the X carriage over the Hemera mounting holes as pictured
* Insert the 2x thin square nuts into the mounting slots if they have fallen out by this point<br>  

---
* Secure the X carriage to the hemera using 4x 10mm bolts, do *not* over tighten<br>  

---
* Get the nozzel fang, undercarriage fan mount, 2x 16mm bolt, 2x Hex Nylon Lock Nut and motor cable
* Make sure the plastic sleeve is removed from the motor cable<br>  

---
* Connect the motor cable and guide it to the back passing behind the pinda<br>  

---
* Insert 2x Hex Nylon Lock Nut onto the undercarriage fan mount using a spare 10mm bolt
* Place the undercarriage fan mount against the nozzel fang and insert 2x 16mm bolts to hold it in place<br>  

---
* Secure the nozzle fang and undercarriage fan mount to the undercarriage assembly as pictured by tightening the 2x 14mm bolts<br>  

---
* Secure the 50mm blower fan using 2x 25mm bolt with 2x M3 washers
* Guide the fan cable the same way as the motor cable<br>  


---
* Secure the motor and fan cable to the undercarraige rigth part using a small zip tie<br>  


---
* Insert the 43mm PTFE tube into the hemera<br>  

---
## Laser Filament Sensor  

 

---
## IR Filament Sensor

30a

---
* Insert the 3mm nylon filament (cable support) into the pictured hole on the undercarraige back part<br>  


---
* Guide the cables in this order through the upper gully on the undercarraige back part
1. Hemera fan cable
2. Filament sensor cable
3. Motor cable
4. Blower fan cable
5. PINDA probe cable<br>  

---
* Slide in the undercarriage back cap taking note of the arrow pointing towards the Hemera<br>  

---
* <br>  
 
 


---
* <br>  

---
* <br>  

---
* <br>  

---
* <br>  

---
* <br>  

---
* <br>  

---
* <br>  

---
[Previous](05_Filament_Sensor.md) | [Next](07_Printer_Assembly.md)

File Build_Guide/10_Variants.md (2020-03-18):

[Previous](10_Fan_Shroud_Fang.md) | [Next](11_Variants.md)

### Parts
|Quantity|Size|Type|
|---:|:---:|:---:|
||mm|M3|

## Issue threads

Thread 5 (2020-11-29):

Fang duct blows too much air on the heated block

tetra3dprint, 2020-11-29:
The fang duct blows too much on the heated block causing a drop in temp when activated.

A sock and pid calibration with the fan on can help mitigate the issue.

tetra3dprint, 2020-11-29:
A modified version is in the works and being tested

ga73, 2021-06-08:
Hi, this looks great! Are there or will there be any updates on this or has it now been discontinued?

tetra3dprint, 2021-06-08:
>
>
> Hi, this looks great! Are there or will there be any updates on this or has it now been discontinued?

I do have an update for this, and it will be dropping within the week!

ga73, 2021-06-08:
Excellent news, top man!    I'll start printing the parts, will there be any other changes apart from the fang duct?

tetra3dprint, 2021-06-08:
>
>
> Excellent news, top man! I'll start printing the parts, will there be any other changes apart from the fang duct?

I would definitely hold out a little bit longer (I will try to drop the parts for/on the weekend), I have an update for the fang, left(motor) and right(idler) parts, z tops and the main x carriage. They are significant in change and are codependent of each other meaning they are not compatible with any of the same previous parts (no mix matching unfortunately)

However the rest of the parts such as the undercarriage assembly(attaches to the hemera directly) remain the same for now and are safe to print before hand.

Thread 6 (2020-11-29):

Extruder cable loom droop

tetra3dprint, 2020-11-29:
The extruder cable loom tends to droop over time and is in danger of hitting the print when not precisely looped in a specific way.

This is exacerbated by third party mainboard cases and frame mods.

tetra3dprint, 2020-11-29:
A new HemeraOdyssey-Undercarriage_Back.stl is in the works and will be released after testing.

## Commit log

2020-03-20 Cable sleve
2020-03-21 Update Print_Settings.md
    Is this what you mean?
2020-03-27 Changed from 6mm to 8mm M3 bolts do to originally being supplied with 6mm M3 in addition to 8mm
    [HemeraOdyssey-Undercarriage_Left.stl, HemeraOdyssey-Undercarriage_Right.stl]
2020-03-27 Updated with changes - 6mm to 8mm undercarraige left and right
2020-07-16 Changed header to connector for clarity
2020-08-04 This fixes the xyz calibraiton fail on z issue
    [HemeraOdyssey-Z_Top_Left_7mm_MK3S.stl, HemeraOdyssey-Z_Top_Left_7mm_MK3S_MK2_5S.stl, HemeraOdyssey-Z_Top_Right_7mm_MK3S.stl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]
2021-01-15 Update Print_Settings.md
    Make the list track easier
2021-01-16 Update BOM_Condensed.md
    1.Rename "Hemera Odyssey BOM Total" to "Hemera Odyssey Beta"
    2.Adjust & sort BOM for easier tracking with an example link.
    3.Remove the "Prerequisite" section since it's included in Original Prusa i3.
    4.Added "printed parts" section in BOM.
2021-06-12 Updated Parts for v01.75
    [HemeraOdyssey-Filament_Sensor_Laser_Housing-01_75.stl, HemeraOdyssey-Filament_Sensor_Laser_Lid-01_75.stl, HemeraOdyssey-Part_Left_Motor-01_75.stl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]
2021-06-12 Fix wrong STLs
    [HemeraOdyssey-Part_Front_Rod_Clamps-01_75.stl, HemeraOdyssey-Part_Right_Front_Rod_Clamp.stl, HemeraOdyssey-Part_Right_Front_Rod_Clamps-01_75.stl]
2021-06-13 Added Rear Rod Wedge
    [HemeraOdyssey-Rear_Rod_Wedge-01_75.stl]
